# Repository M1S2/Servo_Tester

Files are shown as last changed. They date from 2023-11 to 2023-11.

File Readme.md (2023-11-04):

# Servo Tester

This is a simple servo tester PCB.

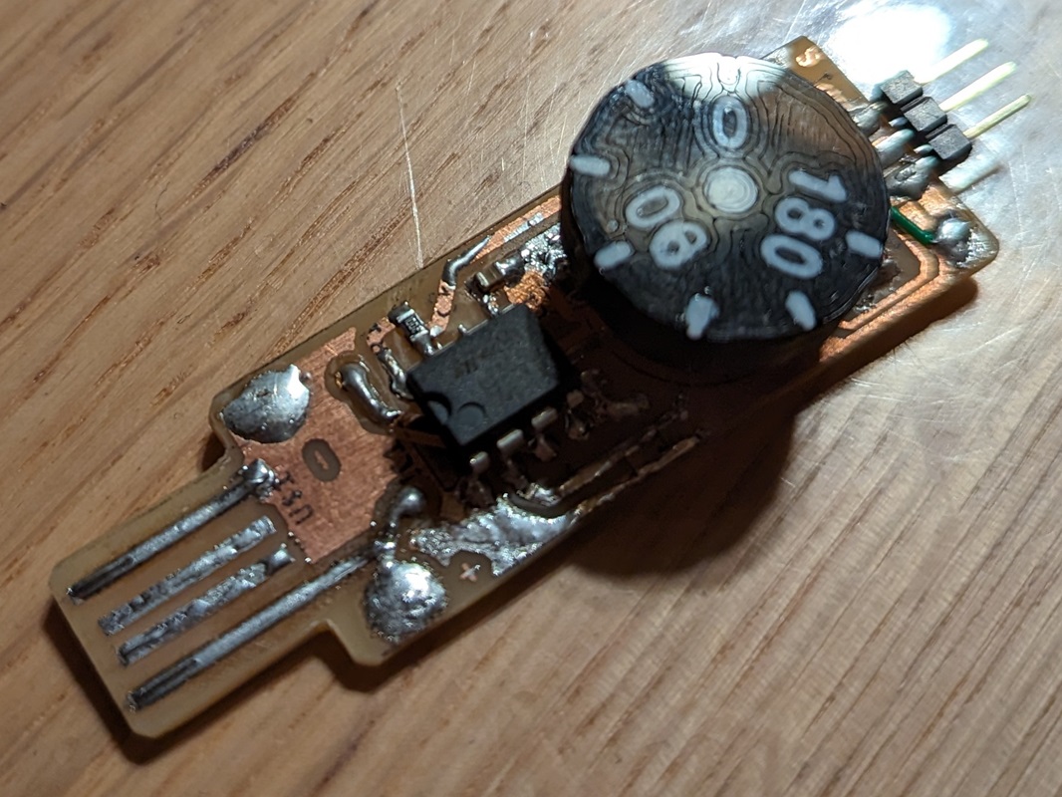
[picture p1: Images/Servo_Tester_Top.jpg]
PCB Top


## PCB
The schematic and PCB are created using Fusion 360. It is designed to be manufactured using toner transfer method so all traces are as big as possible. This is only a one-sided PCB.

## Mechanic
There is no special housing for this servo tester.

The only mechanical parts are:
- USB_Plastic_Plate: a thin plastic plate to ensure the correct thickness of the USB-plug part. The complete thickness including the PCB, solder and the plastic plate should be approx. 2 mm.
- Potentiometer_Knob: a knob for easier operation of the potentiometer. This isn't necessary. The default potentiometer axis can also be used.

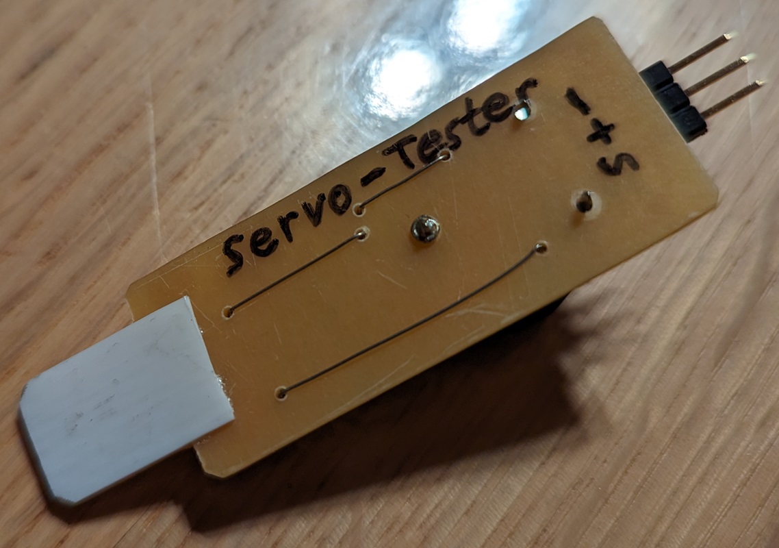
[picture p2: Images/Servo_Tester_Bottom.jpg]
PCB Bottom


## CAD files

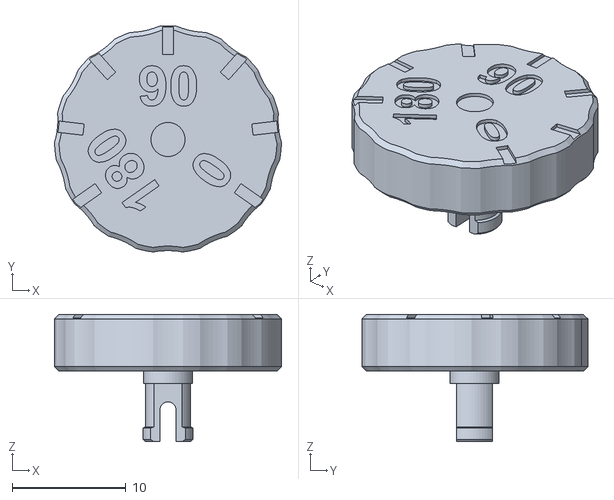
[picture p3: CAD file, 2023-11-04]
Mechanical/Potentiometer_Knob.stl
20.0 x 19.9 x 11.2

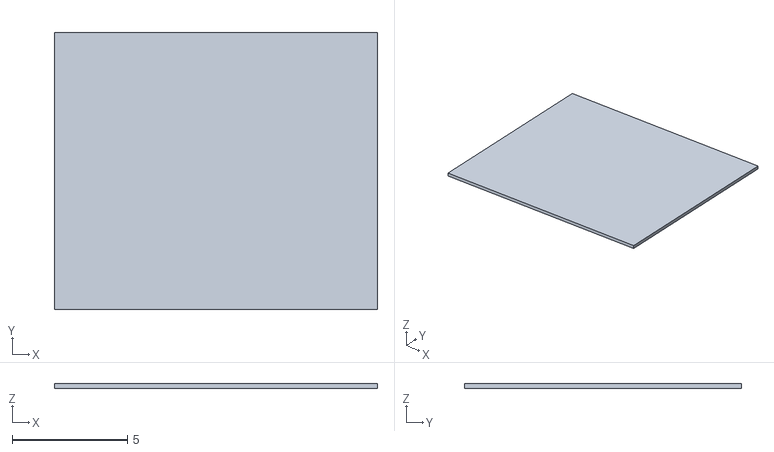
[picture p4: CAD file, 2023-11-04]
Mechanical/USB_Plastic_Plate.stl
14.0 x 12.0 x 0.2

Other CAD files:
Mechanical/Potentiometer_Knob_Font.stl
Mechanical/Potentiometer_Knob.f3d
Mechanical/USB_Plastic_Plate.f3d

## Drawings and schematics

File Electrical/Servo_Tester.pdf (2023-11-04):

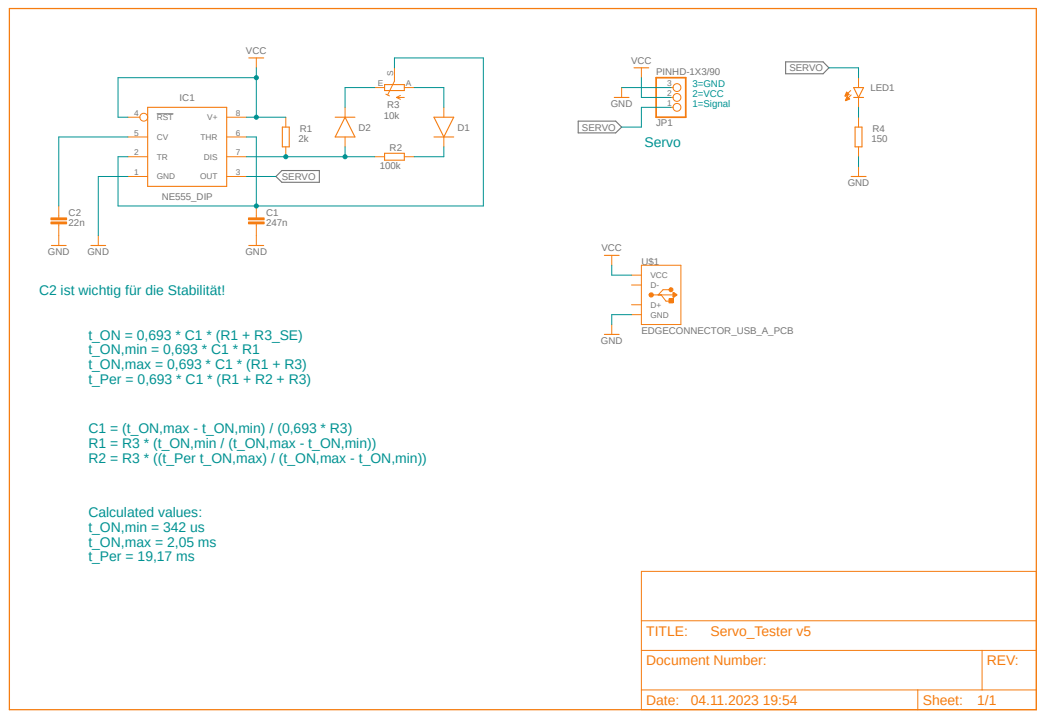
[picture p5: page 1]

C2 ist wichtig für die Stabilität!

Document Number: | REV:

Date: 04.11.2023 19:54 | Sheet: 1/1

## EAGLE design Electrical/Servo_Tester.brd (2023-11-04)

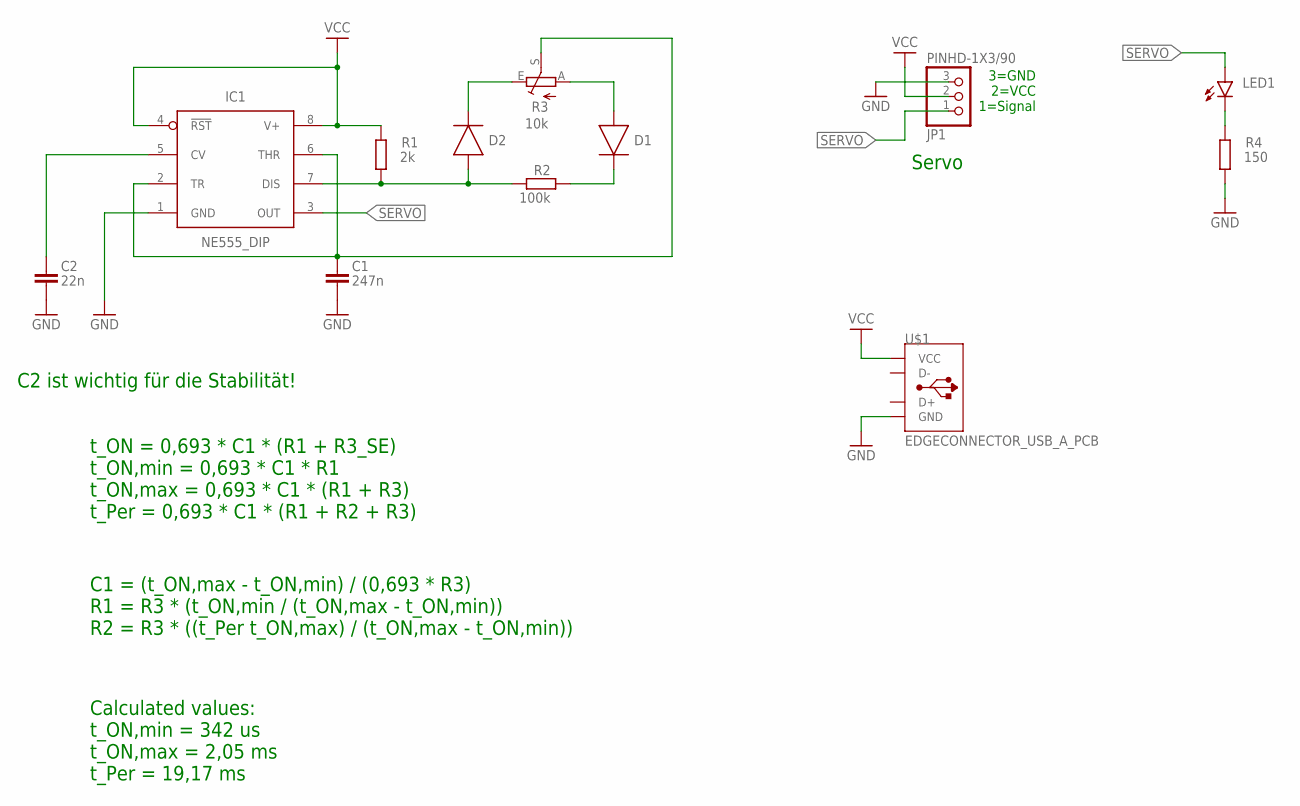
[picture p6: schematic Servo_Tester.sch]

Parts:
C1: 247n; CAPC2012X110
C2: 22n; CAPC2012X110
D1, D2: DIODE_LL4148_SOD-80; DIOMELF3516
IC1: NE555_DIP; DIP826W53P254L959H508Q8B
JP1: PINHD-1X3/90; 1X03/90
LED1: LEDCHIP-LED0805; CHIP-LED0805
R1: 2k; R0805
R2: 100k; R0805
R3: 10k; LI15
R4: 150; R0805
U$1: EDGECONNECTOR_USB_A_PCB

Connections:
GND: C1.2, C2.2, IC1.1 (GND), JP1.3, R4.1, U$1.GND
unnamed: C2.1, IC1.5 (CV)
unnamed: C1.1, IC1.2 (TR), IC1.6 (THR), R3.S
unnamed: D2.2 (A), IC1.7 (DIS), R1.1, R2.1
unnamed: D1.1 (C), R2.2
unnamed: D2.1 (C), R3.E
unnamed: D1.2 (A), R3.A
unnamed: LED1.C, R4.2
SERVO: IC1.3 (OUT), JP1.1, LED1.A
VCC: IC1.4 (!RST), IC1.8 (V+), JP1.2, R1.2, U$1.VCC

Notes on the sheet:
C2 ist wichtig für die Stabilität!
3=GND 2=VCC 1=Signal
Servo
t_ON = 0,693 * C1 * (R1 + R3_SE) t_ON,min = 0,693 * C1 * R1 t_ON,max = 0,693 * C1 * (R1 + R3) t_Per = 0,693 * C1 * (R1 + R2 + R3)
C1 = (t_ON,max - t_ON,min) / (0,693 * R3) R1 = R3 * (t_ON,min / (t_ON,max - t_ON,min)) R2 = R3 * ((t_Per t_ON,max) / (t_ON,max - t_ON,min))
Calculated values: t_ON,min = 342 us t_ON,max = 2,05 ms t_Per = 19,17 ms

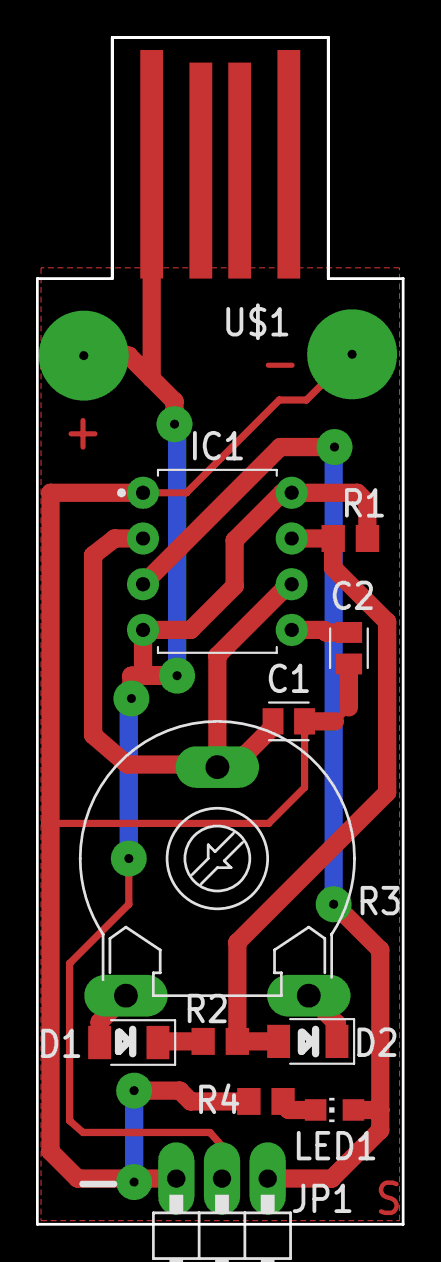
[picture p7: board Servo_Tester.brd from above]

Board: 2 copper layers, 20.3 x 65.9 mm, 12 parts (0 on the bottom side), 10 nets.

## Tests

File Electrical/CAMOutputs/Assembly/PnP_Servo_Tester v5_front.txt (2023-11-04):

C1	13.97	27.94	0.00	247n	CAPC2012X110
C2	17.31	32.00	270.00	22n	CAPC2012X110
D1	5.08	10.10	180.00		DIOMELF3516
D2	15.02	10.16	180.00		DIOMELF3516
LED1	16.51	6.35	90.00		CHIP-LED0805
R1	17.38	38.10	0.00	2k	R0805
R2	10.16	10.16	180.00	100k	R0805
R4	12.70	6.83	0.00	150	R0805
U$1	10.16	58.72	0.00	EDGECONNECTOR_USB_A_PCB	EDGECONNECTOR_USB_A_PCB

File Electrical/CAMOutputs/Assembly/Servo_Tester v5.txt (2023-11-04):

Stückliste exportiert aus Team-Hub: Scheich Projekt: Default Project Leiterplatte: Servo_Tester v5 am 04.11.2023 19:57

Qty Value                   Device                   Package                  Parts  Description                     CATEGORY         CURRENT-SUPPLY DESCRIPTION                      FORWARD_CURRENT FREQUENCY   MANUFACTURER                     MPN          OPERATING_TEMP OPERATING_TEMPERATURE PART_STATUS PITCH   POPULARITY REVERSE_VOLTAGE ROHS_COMPLIANCE ROHS_COMPLIANT  SERIES  SPICEPREFIX SUB-CATEGORY THERMALLOSS TYPE    VALUE      VOLTAGE_RATING
2                           DIODE_LL4148_SOD-80      DIOMELF3516              D1, D2 Diode Rectifier - Popular parts Diode                           DIODE GEN PURP 100V 200MA SOD80                              ON Semiconductor                                                                                                                                                                      Rectifier                        LL4148                   
1                           LEDCHIP-LED0805          CHIP-LED0805             LED1   LED                                                                                                                                                                                                                                 68                                                                                                                                       
1   100k                    R-EU_R0805               R0805                    R2     RESISTOR, European symbol                                                                                                                                                                                                           86                                                                 R                                                                     
1   10k                     TRIM_EU-LI15             LI15                     R3     POTENTIOMETER                                                                                                                                                                                                                       0                                                                                                                                        
1   150                     R-EU_R0805               R0805                    R4     RESISTOR, European symbol                                                                                                                                                                                                           86                                                                 R                                                                     
1   22n                     C_CHIP-0805(2012-METRIC) CAPC2012X110             C2     Capacitor - Generic             Capacitor                                                                                                                                                                                                                                                                                                                                    
1   247n                    C_CHIP-0805(2012-METRIC) CAPC2012X110             C1     Capacitor - Generic             Capacitor                                                                                                                                                                                                                                                                                                                                    
1   2k                      R-EU_R0805               R0805                    R1     RESISTOR, European symbol                                                                                                                                                                                                           86                                                                 R                                                                     
1   EDGECONNECTOR_USB_A_PCB EDGECONNECTOR_USB_A_PCB  EDGECONNECTOR_USB_A_PCB  U$1                                                                                                                                                                                                                                                                                                                                                                                 
1   NE555_DIP               ICM7555_DIP              DIP826W53P254L959H508Q8B IC1    TIMER                           IC_Clock-Timing  60µA           IC OSC SINGLE TIMER 1MHZ 8DIP                    1MHz        Renesas Electronics America Inc  ICM7555IPAZ  -25°C to 85°C                        Active                                                         ROHS3 Compliant                     Timer                                                     
1   PINHD-1X3/90            PINHD-1X3/90             1X03/90                  JP1    PIN HEADER                      Headers                         Header                            Right Angle     3 Position                                               Generic        Generic                           Generic Active     0.100" (2.54mm)                                 Generic             Generic                  Headers  Male Pins

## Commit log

2023-11-04 Initial version tracked by GIT (milestone V1.0) in Fusion360
    [Potentiometer_Knob.f3d, Potentiometer_Knob.stl, Potentiometer_Knob_Font.stl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]
2023-11-04 Added LED to PCB, slightly adapted some texts
    [Servo_Tester.brd, Servo_Tester.sch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]
